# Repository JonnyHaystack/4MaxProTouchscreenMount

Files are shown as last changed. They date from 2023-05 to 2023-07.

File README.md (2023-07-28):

# 4MaxProTouchscreenMount
Parametric and modular touchscreen mount for Anycubic 4Max Pro (2.0)

## Background

I switched to using the Klipper firmware on my 4Max Pro 2.0 a while back, and if you've ever used Klipper, I'm sure you understand why I can never go back to Marlin. The one feature of this printer that doesn't work with Klipper is the touchscreen, which is some proprietary thing with very limited functionality, and I never liked it even when it did work. Fortunately, at the same time I started using Klipper, I learned of the existence of [KlipperScreen](https://klipperscreen.readthedocs.io/en/latest/), which provides much more functionality and a prettier UI.

However, KlipperScreen requires a custom touchscreen directly connected to the Klipper host, which means I had to do some extra work. In KlipperScreen's [list of supported hardware](https://klipperscreen.readthedocs.io/en/latest/Hardware/), there is a 3.5" Raspberry Pi touchscreen, which happens to be the same size as the stock touchscreen in the 4Max Pro. These are very inexpensive and easy to obtain from AliExpress or Amazon, and are a convenient solution if you already use a Pi as your Klipper host. After procrastinating for a year, I started by opening up the printer and taking some measurements and designing a replica of the stock touchscreen mount. I then printed it out, verified it against the original, and proceeded to create a modified design for the mounting plate to accomodate this Raspberry Pi touchscreen. As for the wiring, to keep it relatively simple, I used a 2x13 pin ribbon cable (2.54mm pitch of course).

I recommend at least 1 metre length, if you plan on installing your Pi inside the bottom of the printer, or longer if you want to keep it separate. I also had to clip off some of the casing of the female end of the connector to get it to fit, and bend some of the GPIO pins on the Raspberry Pi in order to get the male connector to fit, but those were very minor inconveniences to me.

## Off-the-shelf hardware

| Part | Link | Price | Quantity |
| ---- | ---- | ----- | --- |
| Ribbon cable (length 1M, A-02, 2x13 26P) | https://www.aliexpress.com/item/1005003733065114.html | £6 | 1 |
| Raspberry Pi 3.5" touchscreen | https://www.aliexpress.com/item/32229578580.html | £7 | 1 |
| M2 self-tapping screws (around 4-8mm length) | You can find them anywhere | Cheap | 4 |

## 3D printed hardware

| Part | Quantity |
| ---- | --- |
| 4Max_Pro_RPi_Touchscreen_Mount_Plate | 1 |
| 4Max_Pro_RPi_Touchscreen_Mount_Spacer | 4 |

The plate and spacers are separate to enable easy FDM printing without supports. These parts are all best printed in their default orientation (flat side down).

## Installation

1. Prepare the new touchscreen mount by securing the 3D printed spacers to the 3D printed mounting plate using the M2 self-tapping screws, connecting the ribbon cable to the Raspberry Pi touchscreen in the orientation shown below, and placing the touchscreen onto the spacers. It should friction fit and be held securely, but not be bent by excessive pressure. Ignore the chopped off bits of the 3D printed plate - I have improved the design since installing it for myself. You will probably need to clip the plastic on the female end of the ribbon cable to get it to fit around the plate. It's very soft plastic and easy to do this without any negative effects.



2. Remove all panels from the printer. You must remove the bottom panel first, then the rear panel, followed by the side panels, and then the top panel. You should disconnect the cable from the stock touchscreen before removing the top panel. The final panel is the front panel, which you only need to remove if you want to route your wiring through the front, which is what I found to be the cleanest way. Removing the side panels is the most difficult part, because there are multiple plastic latches you need to move out of the way with some kind of prying tool while applying constant outward pressure to the panel so the latches don't slide back into place.
3. Unfasten the 4 screws that secure the stock touchscreen mounting plate to the top panel. This allows you to remove the stock touchscreen from the printer frame.
4. Use the screws from the stock touchscreen mount to secure the new touchscreen mount to the frame. Refer to the image in step 1 for orientation.
5. Route your ribbon cable to your Raspberry Pi somehow. Below are photos of how I achieved this by routing the cable down the side of the front panel. It required cutting off a little bit of the bottom of the front panel to fit the cable through into the underside of the printer's frame.




The wiring and the cut parts of the front panel are completely hidden once the bottom panel is secured, so don't worry too much about it looking ugly!

6. Put the printer back together. For convenience, I have catalogued which screws are used for which panels below.

- 8x M3x6 cap head for front panel
- 9x M3x6 cap head for top panel
- 8x M3x4 countersunk for side panels
- 8x M3x10 countersunk for back panel
- 4x M3x10 cap head for bottom panel
- 4x M4x8 cap head for bottom panel
- 4x M3x12 pan head wood screws for touchscreen

## Software Configuration

See the [KlipperScreen documentation](https://klipperscreen.readthedocs.io) for setting up KlipperScreen itself, and see the [LCD Wiki page](http://www.lcdwiki.com/3.5inch_RPi_Display) for the 3.5" Raspberry Pi touchscreen for driver setup and calibration.

For the orientation in which I installed the touchscreen, I had to first apply the rotation of the display as instructed on the LCD Wiki page, and then create the following file in `/etc/X11/xorg.conf.d/99-calibration.conf`, in order to transform the touchscreen inputs to match the display rotation.
```
Section "InputClass"
        Identifier      "calibration"
        MatchProduct    "ADS7846 Touchscreen"
        Option "TransformationMatrix" "-1 0 1 0 1 0 0 0 1"
        #Option  "Calibration"   "3936 227 268 3880"
        #Option  "SwapAxes"      "1"
EndSection
```

In order for this config to be applied you must restart the Raspberry Pi or at least restart Xorg.

## Final result

Have fun!



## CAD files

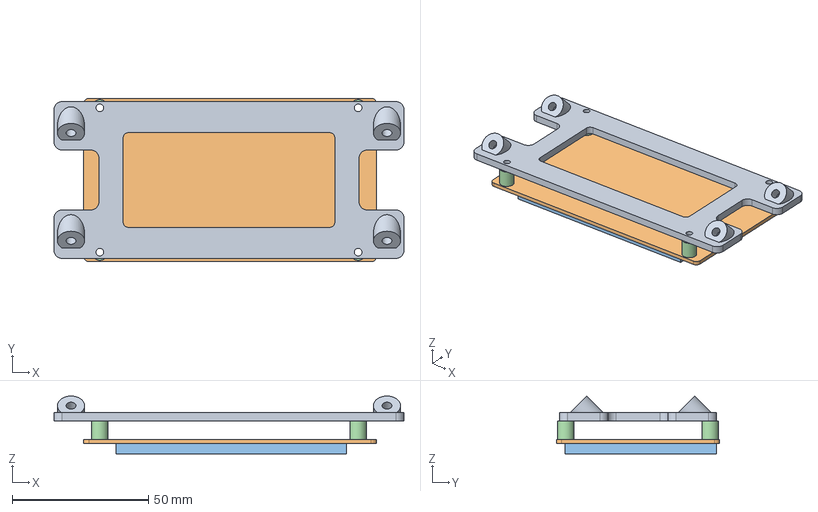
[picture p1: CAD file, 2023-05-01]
STEP/4Max_Pro_Stock_Touchscreen_Mount.step
128.5 x 60.0 x 21.3 mm

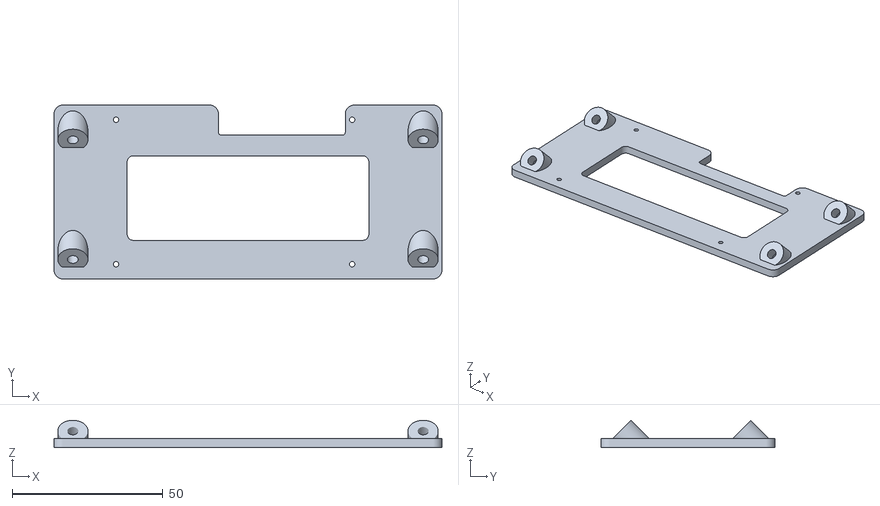
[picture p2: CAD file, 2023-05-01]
STL/4Max_Pro_RPi_Touchscreen_Mount_Plate.stl
128.5 x 57.6 x 9.08

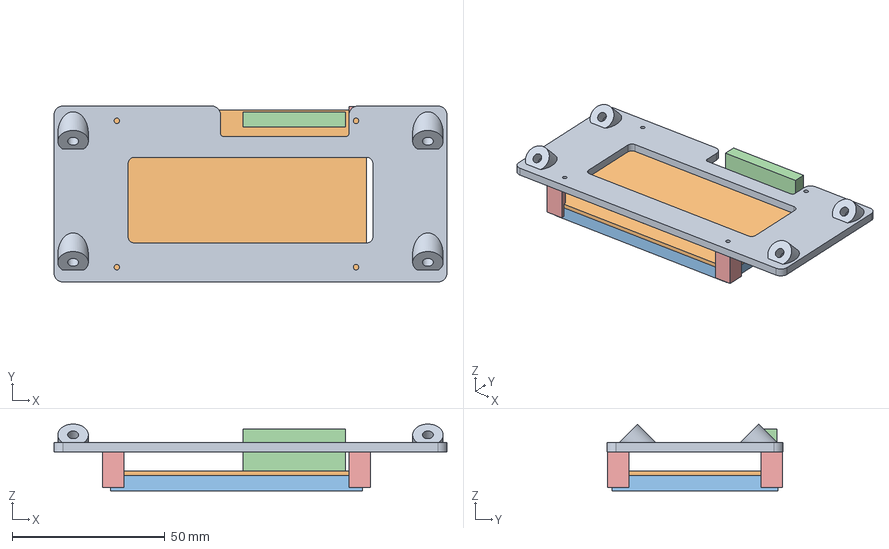
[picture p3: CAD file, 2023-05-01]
STEP/4Max_Pro_RPi_Touchscreen_Mount.step
128.5 x 57.6 x 21.9 mm

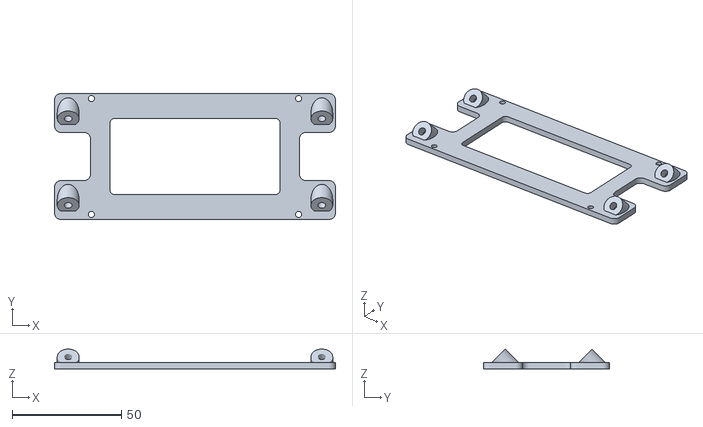
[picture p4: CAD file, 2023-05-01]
STL/4Max_Pro_Stock_Touchscreen_Mount_Plate.stl
128.5 x 57.6 x 9.08

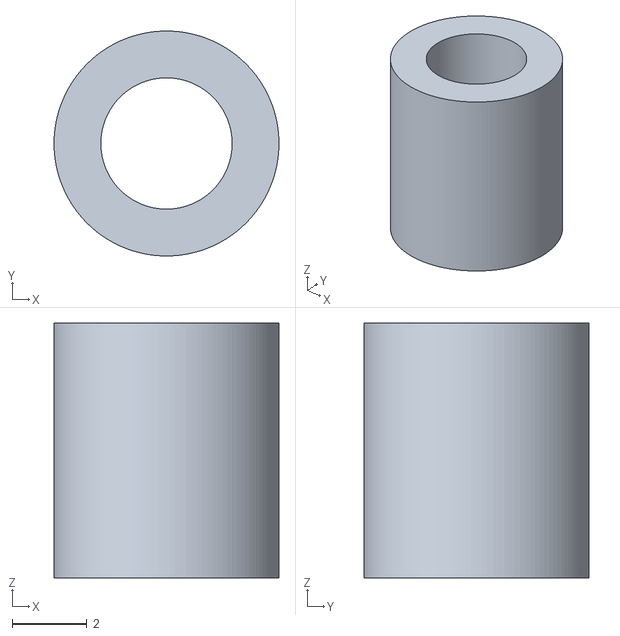
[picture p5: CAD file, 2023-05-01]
STL/4Max_Pro_Stock_Touchscreen_Mount_Spacer.stl
6.00 x 6.00 x 6.80

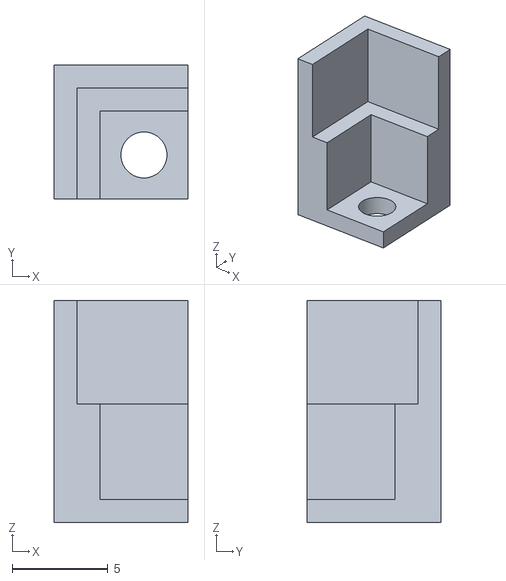
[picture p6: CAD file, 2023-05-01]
STL/4Max_Pro_RPi_Touchscreen_Mount_Spacer.stl
7.00 x 7.00 x 11.6

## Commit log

2023-04-25 Replace PCB standoffs with separate spacer part
2023-04-26 Update to use Joints and assembly
2023-04-28 Clean up pcb_screw_locations
2023-04-29 Clean up and add joints to PCB
2023-04-29 Add LCD to PCB and convert to assembly
2023-04-30 Finish RPi touchscreen PCB assembly
2023-04-30 Design spacer for RPi touchscreen
2023-04-30 Fix RPi touchscreen mounting height
2023-05-01 Mostly finish RPi touchscreen mount
2023-05-01 Offset RPi touchscreen by 4.65mm to the right
2023-05-01 Add STEP and STL files
    [4Max_Pro_RPi_Touchscreen_Mount.step, 4Max_Pro_RPi_Touchscreen_Mount_Plate.stl, 4Max_Pro_RPi_Touchscreen_Mount_Spacer.stl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]
2023-05-01 Reduce plate height because of clearance issue
    [4Max_Pro_RPi_Touchscreen_Mount.step, 4Max_Pro_RPi_Touchscreen_Mount_Plate.stl, 4Max_Pro_Stock_Touchscreen_Mount.step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]
